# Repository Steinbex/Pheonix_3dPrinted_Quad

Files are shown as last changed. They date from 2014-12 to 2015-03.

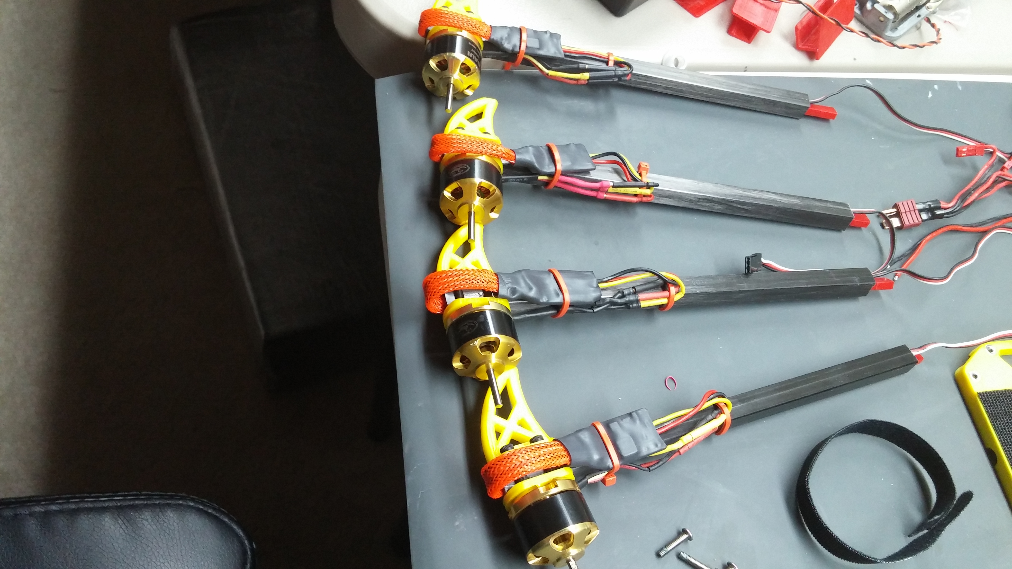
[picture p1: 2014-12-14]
Manual/Images/20141213_224951.jpg

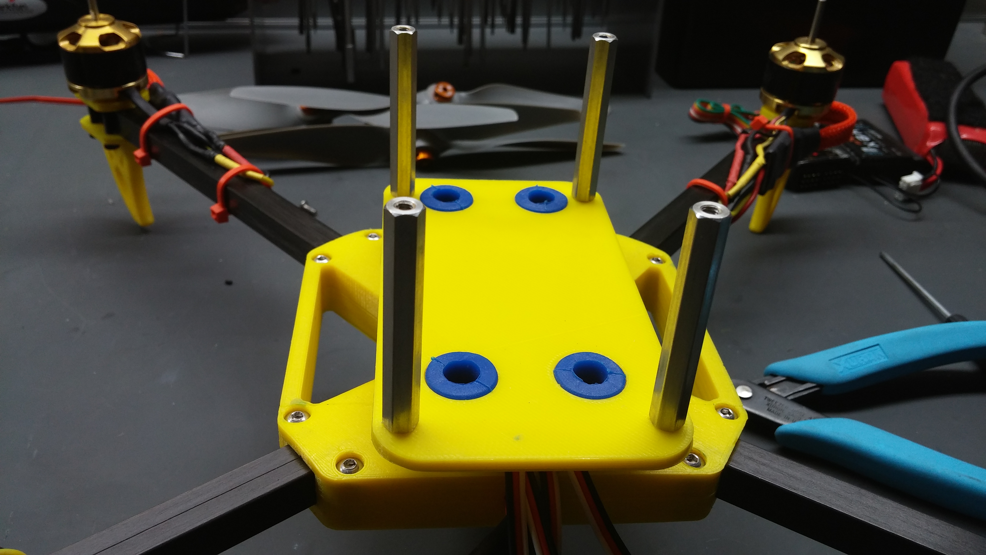
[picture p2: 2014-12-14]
Manual/Images/20141213_233334.jpg

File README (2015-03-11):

Here is the quad frame that, along with a 3d printer, never dies. This durable frame is the result of about a dozen iterations that have led to this lightweight, clean and dirty plate design, that can be built with nearly all 3d printed components. I release it here under the apache license with the intent that we can all grow this together to try and make a constantly improving quad. 

To BUILD:
Print 
4x bottom motor mounts
4x top motor mounts
1x Center Section-1
1x Center Section-2 

For FPV Add:
1x Center Section-1
1x Center Section-2

Non-Printed Hardware:
Main Frame:
16x m3x0.5x18mm Socket Head Cap Screws McMaster 92095A472 for the motor mounts
15x m3x0.5x14mm Socket Head Cap Screws McMaster 92095A168 for the center section
15x m3x0.5 Hex Nut McMaster 90591A121
4x 10mmx200mm Carbon Square Tube Hobbyking 0780000006-0

Clean Plate:
8x M3x0.5x6mm Socket head cap screws McMaster 92095A179 for attaching the plates to the standoffs
4x M3 x 45mm Standoffs McMaster 95947A272 for Clean Plate
4x Vibration Dampeners Hobbyking 450000030-0 for clean plate

Recommended flying specs:
3s 2200 maH Lipo battery
1100 kv Motors
10-15a speed controllers
8x4.5 props

TODO:
More complete Mechanical BOM
Electrical BOM

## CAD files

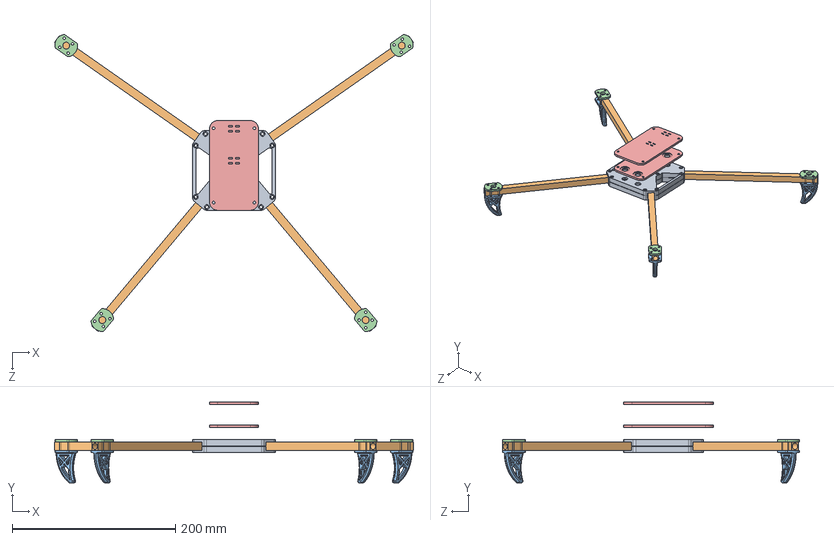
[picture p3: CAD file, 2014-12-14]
Model Files/Pheonix Quad.SLDASM
439.9 x 99.0 x 363.8 mm
Center Section x 2
Carbon Arm x 4
Bottom Motor Mount x 4
Top Motor Mount x 4
Clean Plate x 2

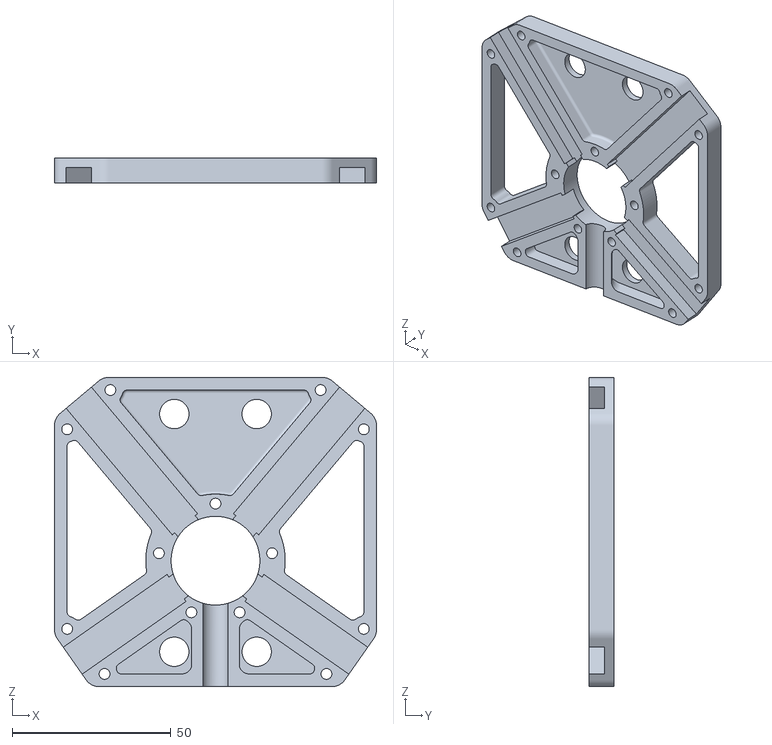
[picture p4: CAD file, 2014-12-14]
Build Files/Carbon Arm Quad - Center Section-2.STL
101.6 x 7.75 x 97.6

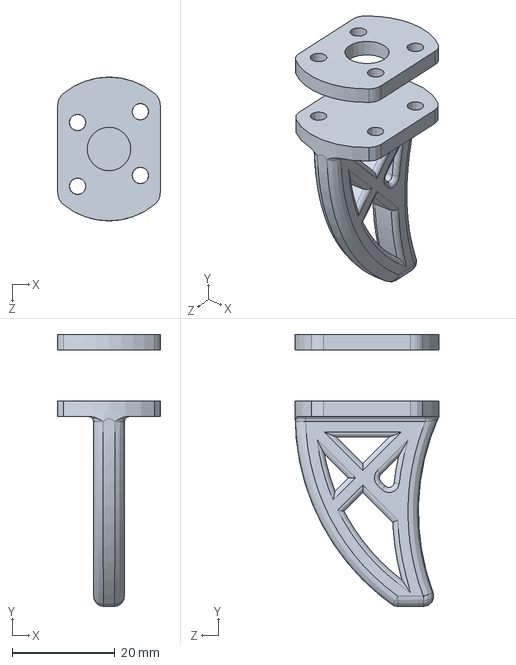
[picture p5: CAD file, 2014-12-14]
Model Files/V2 Motor Mount.SLDPRT
20.0 x 53.0 x 28.0 mm

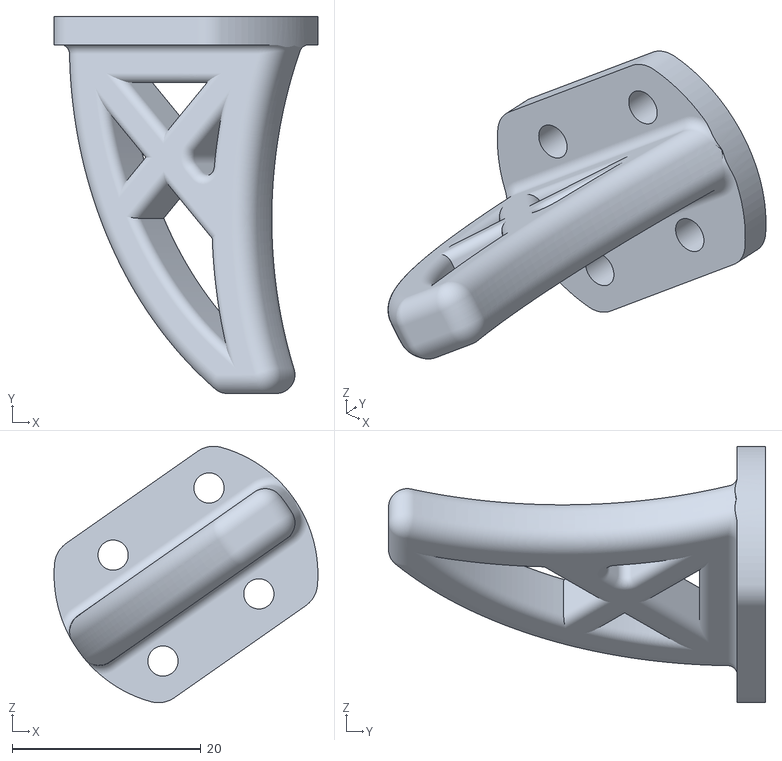
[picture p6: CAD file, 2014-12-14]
Build Files/Carbon Arm Quad - Bottom Motor Mount-1.STL
28.0 x 40.0 x 27.2

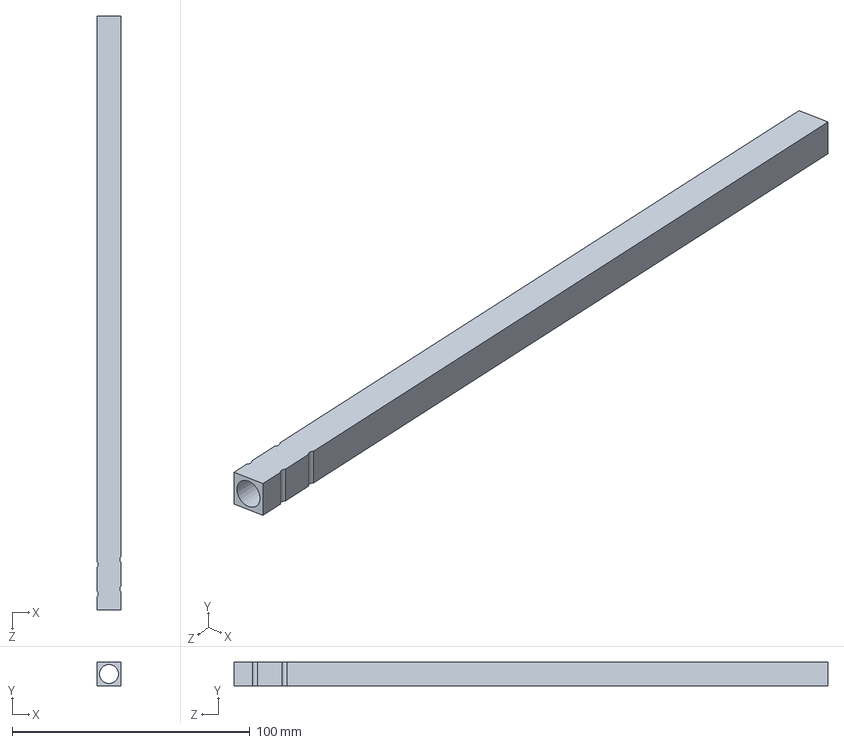
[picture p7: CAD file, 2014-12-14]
Model Files/Carbon Arm.SLDPRT
10.0 x 10.0 x 250.0 mm

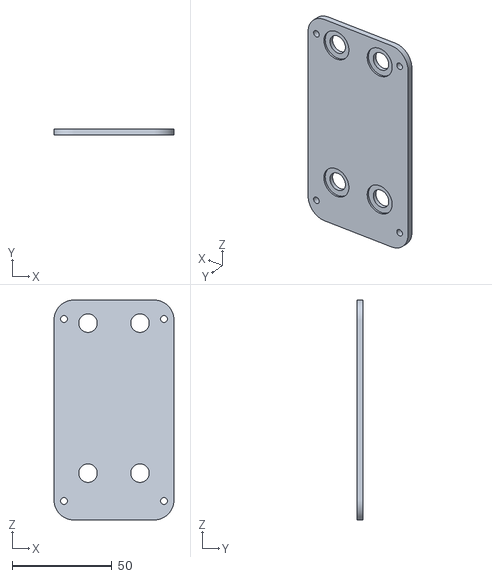
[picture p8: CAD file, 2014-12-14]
Build Files/Carbon Arm Quad - Clean Plate-1.STL
60.0 x 3.00 x 110.0

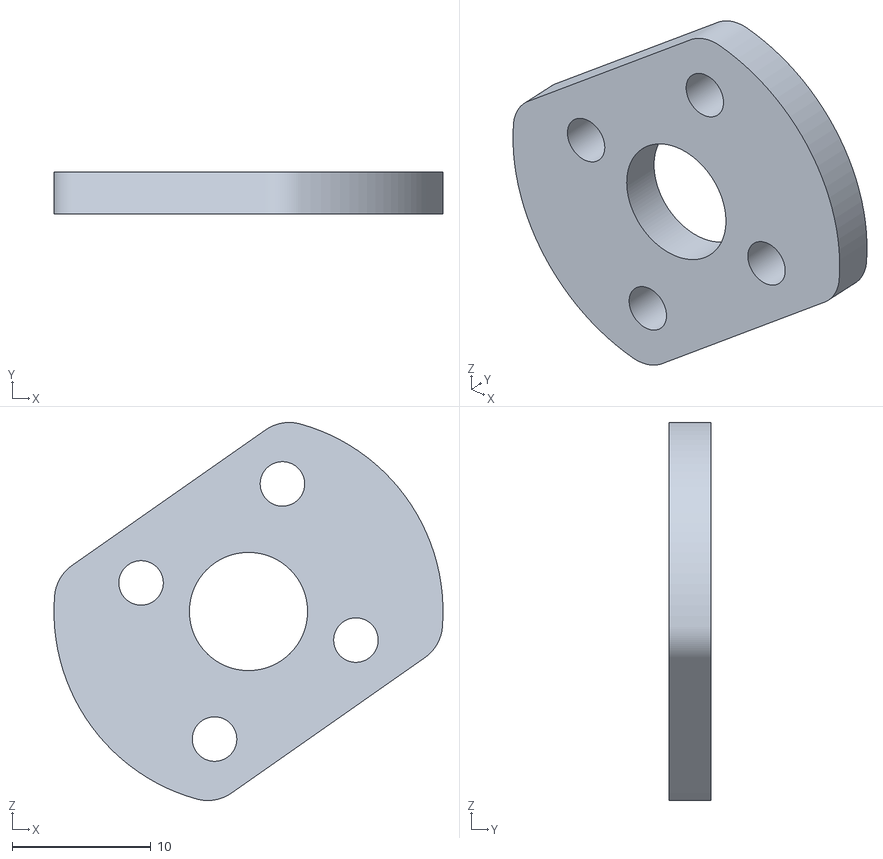
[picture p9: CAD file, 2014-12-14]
Build Files/Carbon Arm Quad - Top Motor Mount-1.STL
28.0 x 3.00 x 27.2

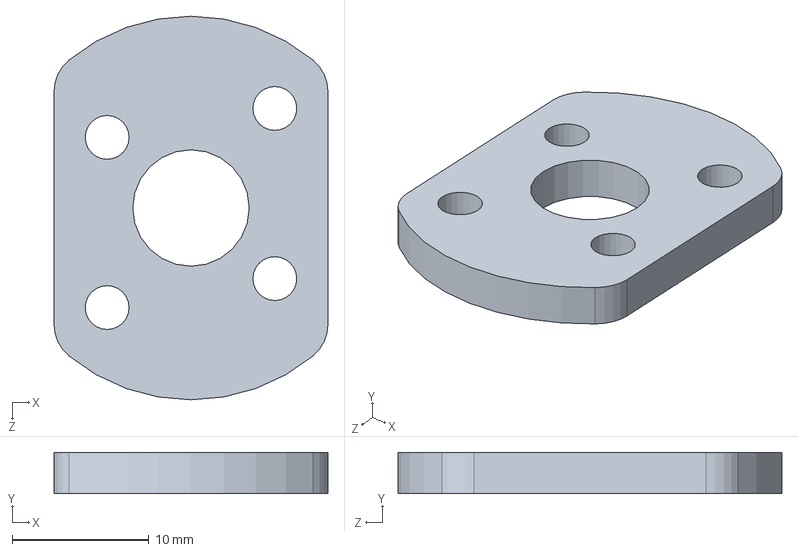
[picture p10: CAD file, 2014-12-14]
Model Files/Top Motor Mount.sldprt
20.0 x 3.00 x 28.0 mm

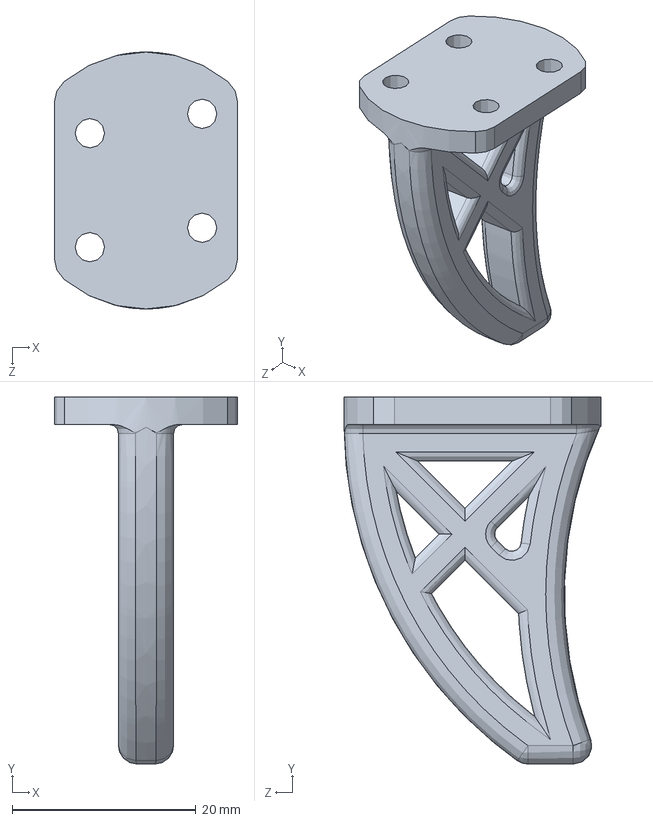
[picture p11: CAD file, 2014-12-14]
Model Files/Bottom Motor Mount.sldprt
20.0 x 40.0 x 28.0 mm

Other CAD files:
Model Files/Clean Plate.SLDPRT
Build Files/Carbon Arm Quad - Center Section-1.STL
Build Files/Carbon Arm Quad - Clean Plate-2.STL
Model Files/Center Section.SLDPRT

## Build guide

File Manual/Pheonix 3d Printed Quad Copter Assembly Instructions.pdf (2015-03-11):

# Pheonix 3d Printed Quad Copter Assembly Instructions

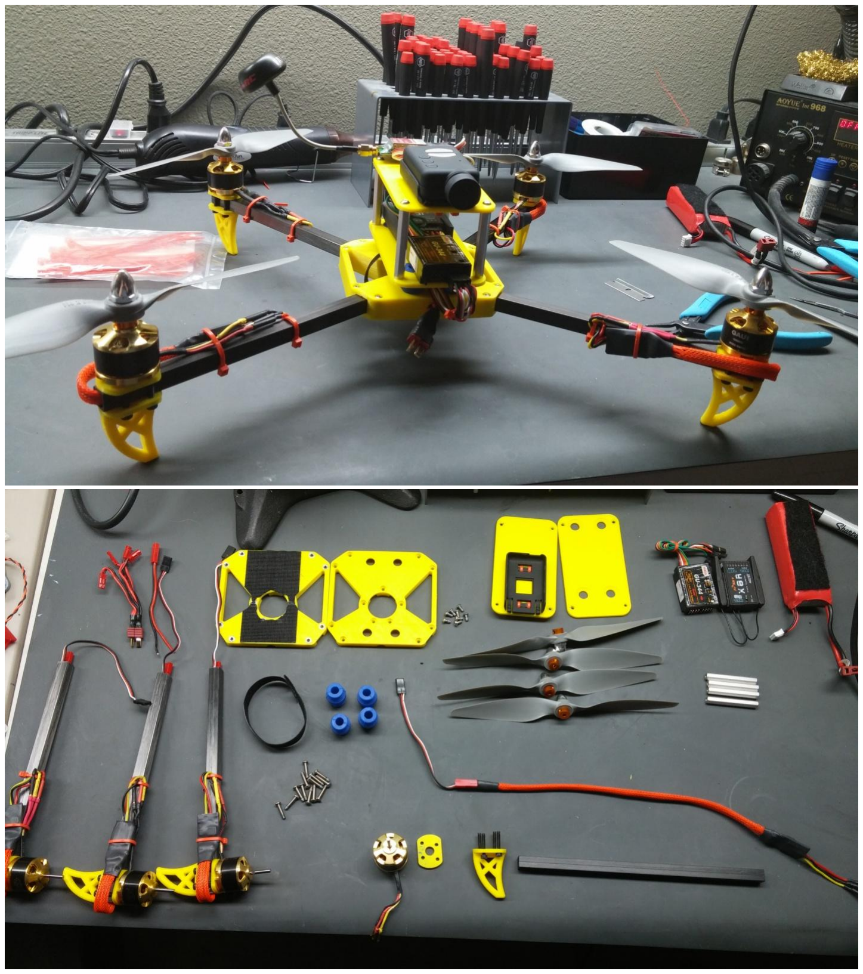
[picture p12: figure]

### Arm Assembly:

To begin the assembly we will start by assembling one of the arms. Start by taking one of the carbon booms and, using a rat tail file make clearance for the screws to go around the bar as in the picture.

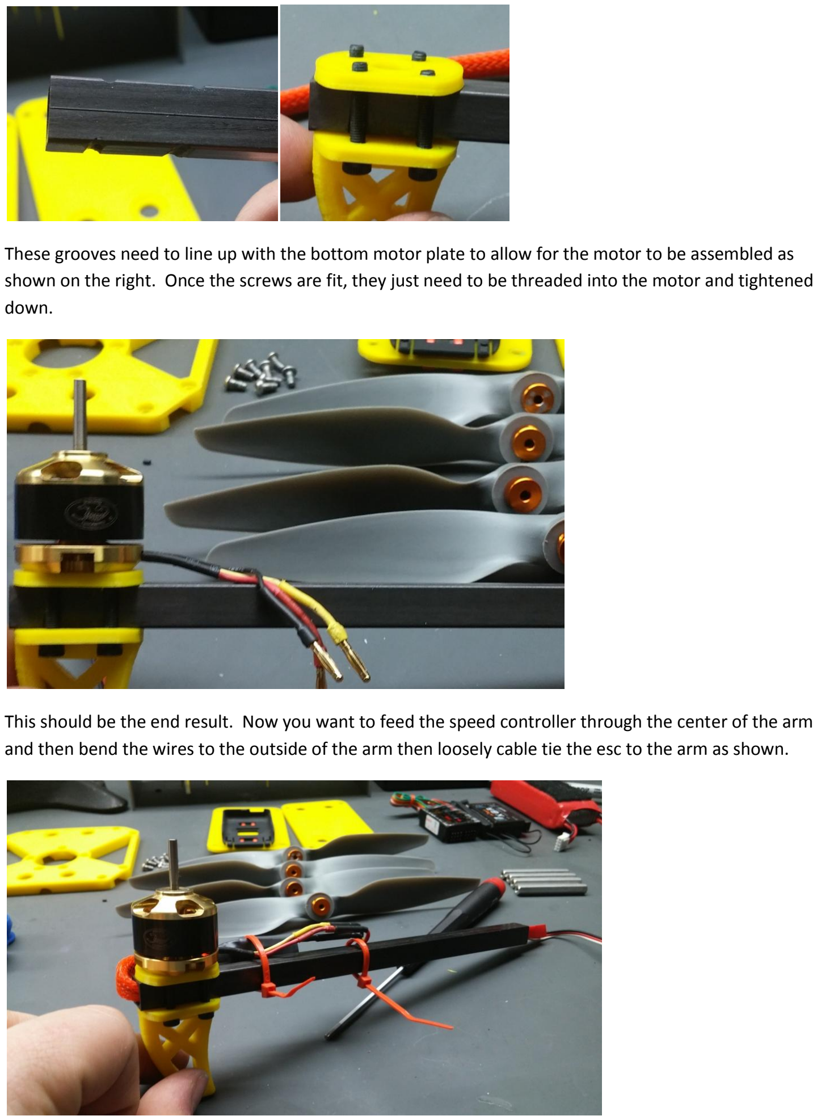
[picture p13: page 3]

These grooves need to line up with the bottom motor plate to allow for the motor to be assembled as shown on the right. Once the screws are fit, they just need to be threaded into the motor and tightened down.

This should be the end result. Now you want to feed the speed controller through the center of the arm and then bend the wires to the outside of the arm then loosely cable tie the esc to the arm as shown.

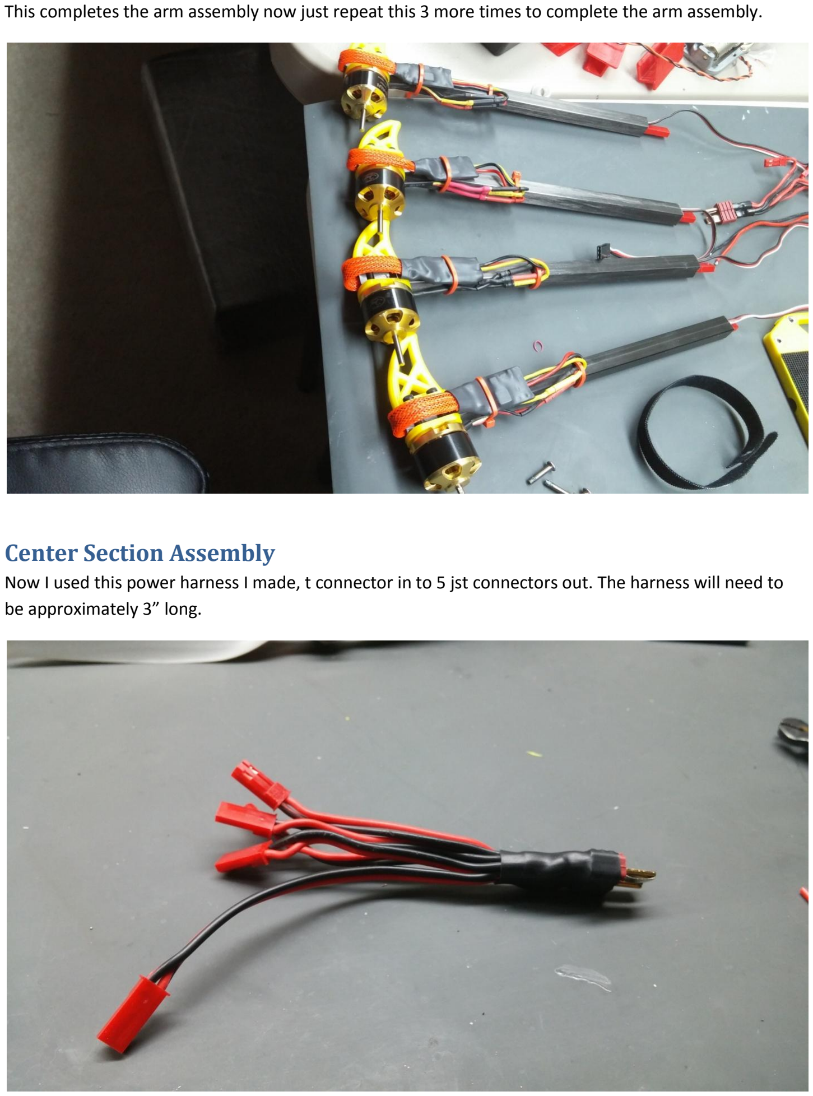
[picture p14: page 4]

This completes the arm assembly now just repeat this 3 more times to complete the arm assembly.

### Center Section Assembly

Now I used this power harness I made, t connector in to 5 jst connectors out. The harness will need to be approximately 3” long.

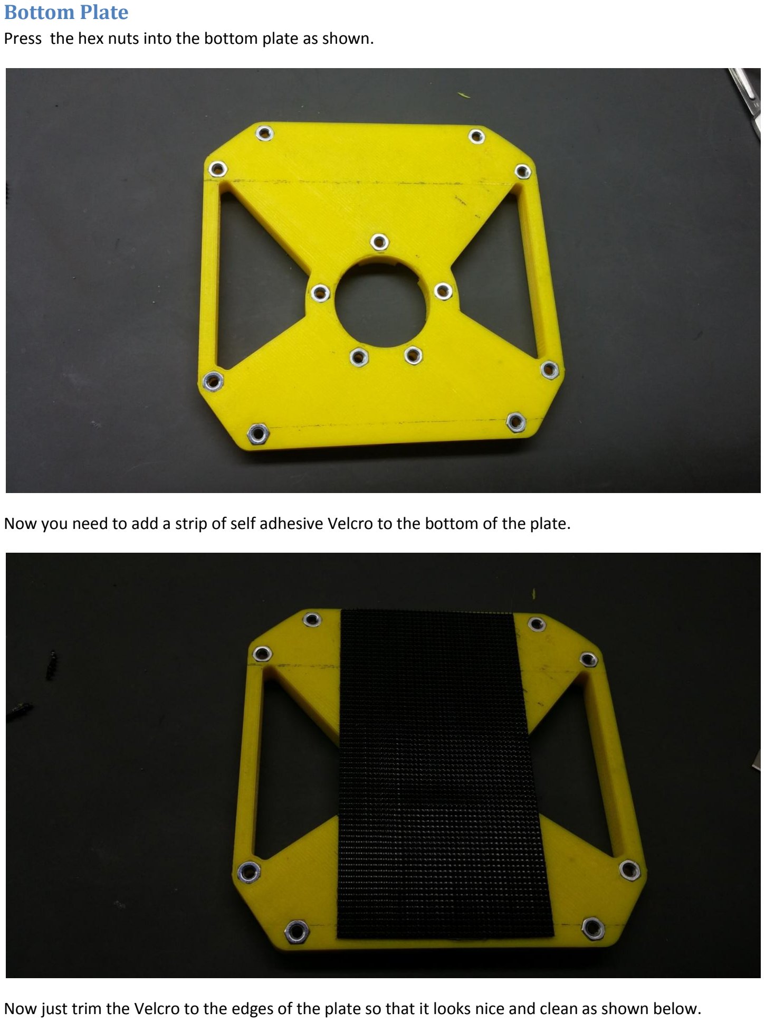
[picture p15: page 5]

### Bottom Plate

Press the hex nuts into the bottom plate as shown.

Now you need to add a strip of self adhesive Velcro to the bottom of the plate.

Now just trim the Velcro to the edges of the plate so that it looks nice and clean as shown below.

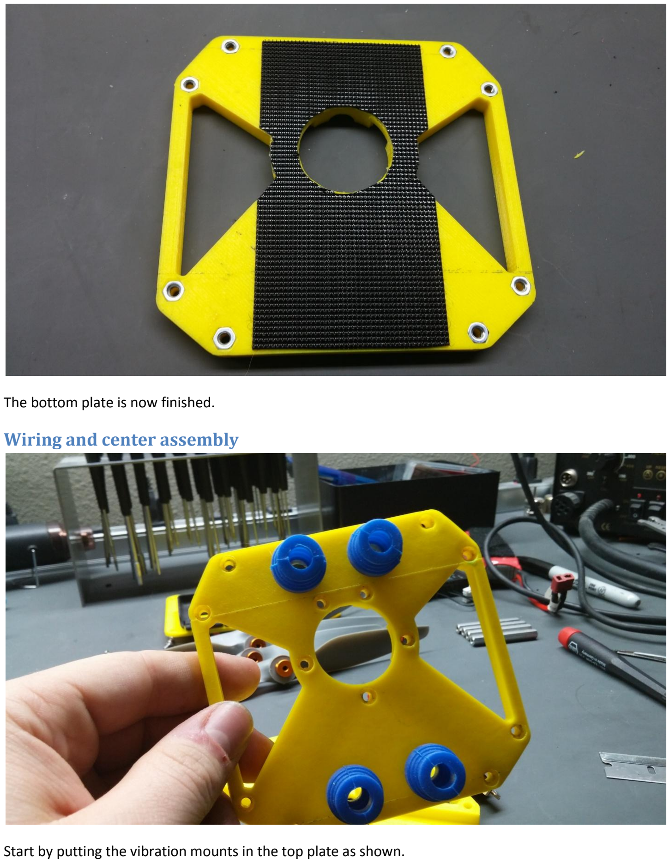
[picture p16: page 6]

The bottom plate is now finished.

### Wiring and center assembly

Start by putting the vibration mounts in the top plate as shown.

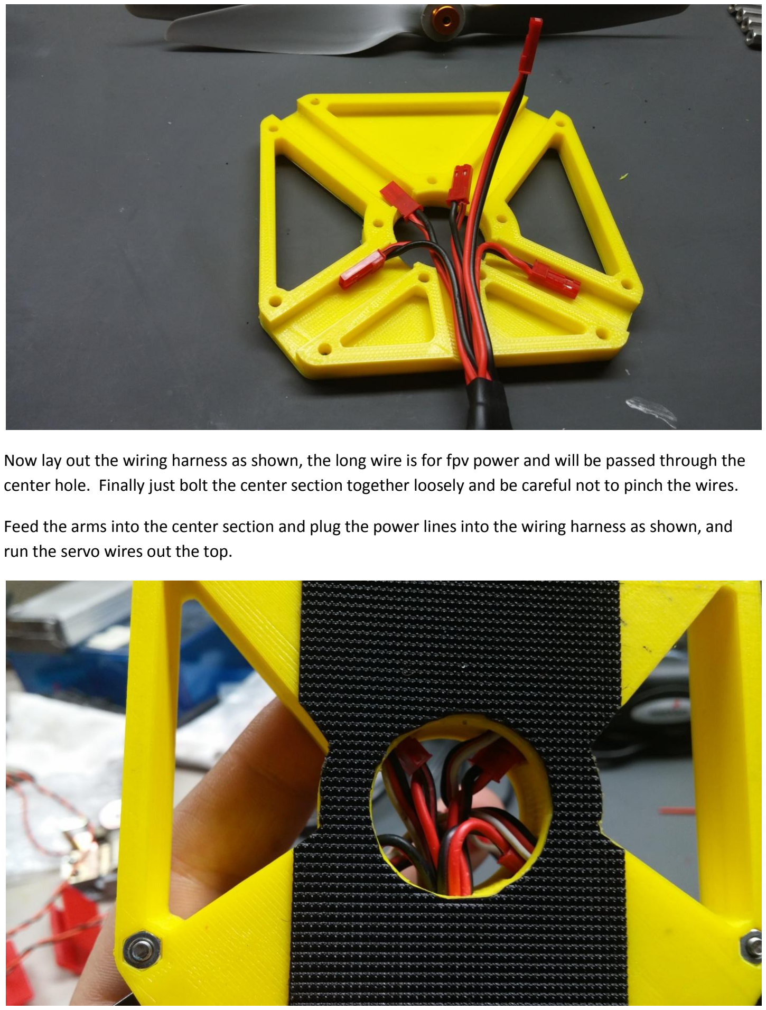
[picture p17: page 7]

Now lay out the wiring harness as shown, the long wire is for fpv power and will be passed through the center hole. Finally just bolt the center section together loosely and be careful not to pinch the wires.

Feed the arms into the center section and plug the power lines into the wiring harness as shown, and run the servo wires out the top.

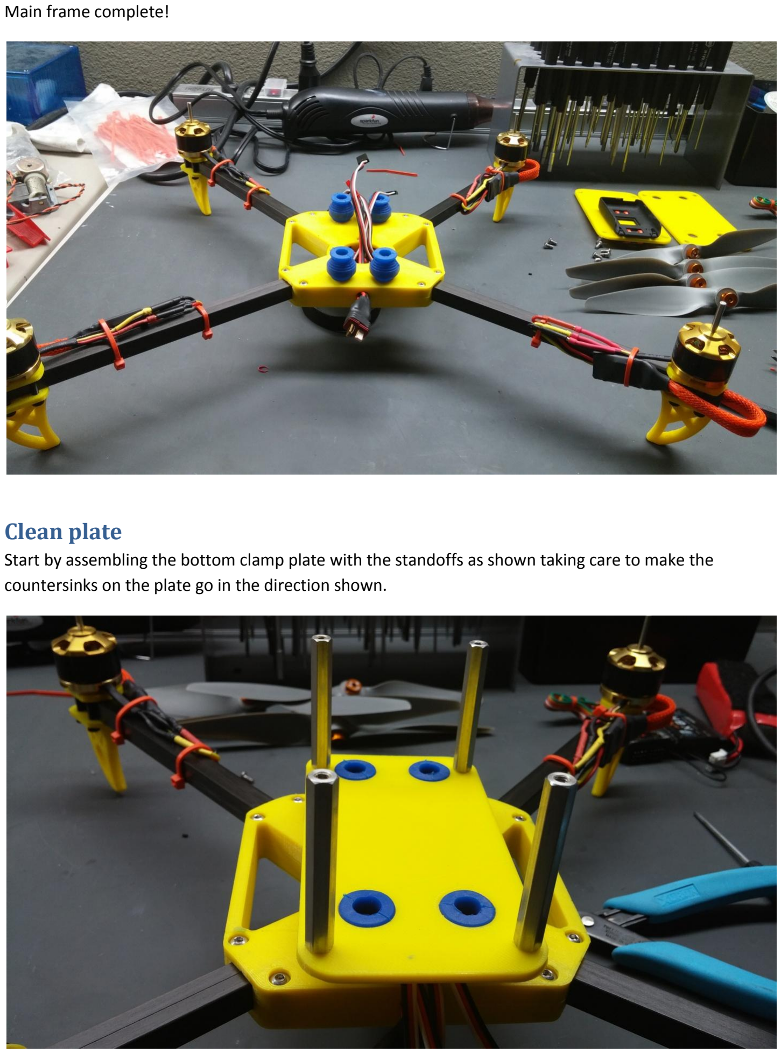
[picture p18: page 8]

Main frame complete!

### Clean plate

Start by assembling the bottom clamp plate with the standoffs as shown taking care to make the countersinks on the plate go in the direction shown.

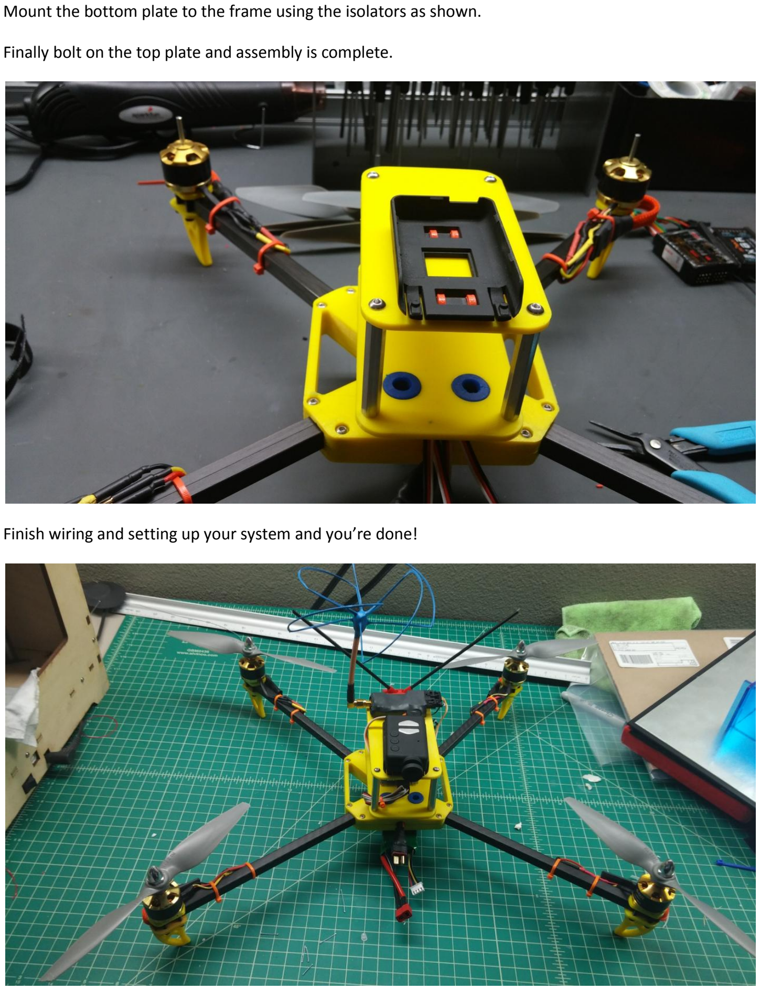
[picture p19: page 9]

Mount the bottom plate to the frame using the isolators as shown.

Finally bolt on the top plate and assembly is complete.

Finish wiring and setting up your system and you’re done!

### Updates:

1. Since the initial build I have now switched the arms to the woven carbon arms found on rcexplorer.se and it is much more tough. There are no changes to the instructions.
2. The Gaui controller is antiquated, and I knew that from the beginning. I have since switched to the Naze32 which is so much better, just solid and reliable.

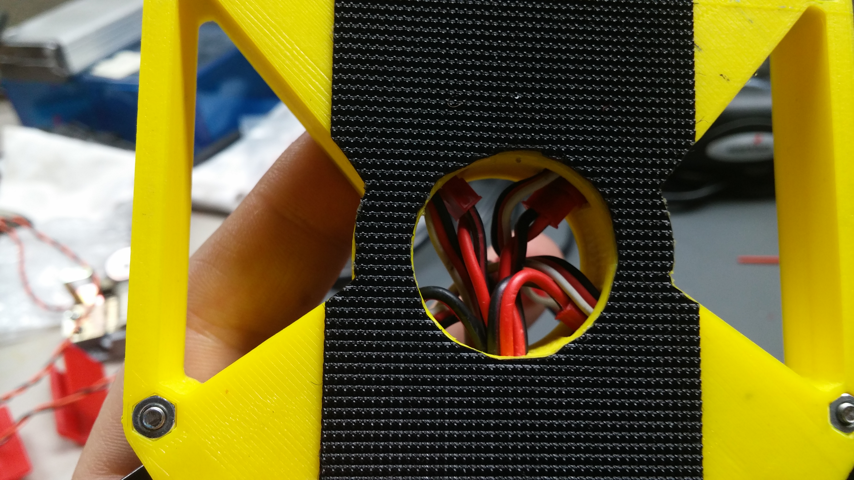
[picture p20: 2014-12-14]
Manual/Images/20141213_232949.jpg

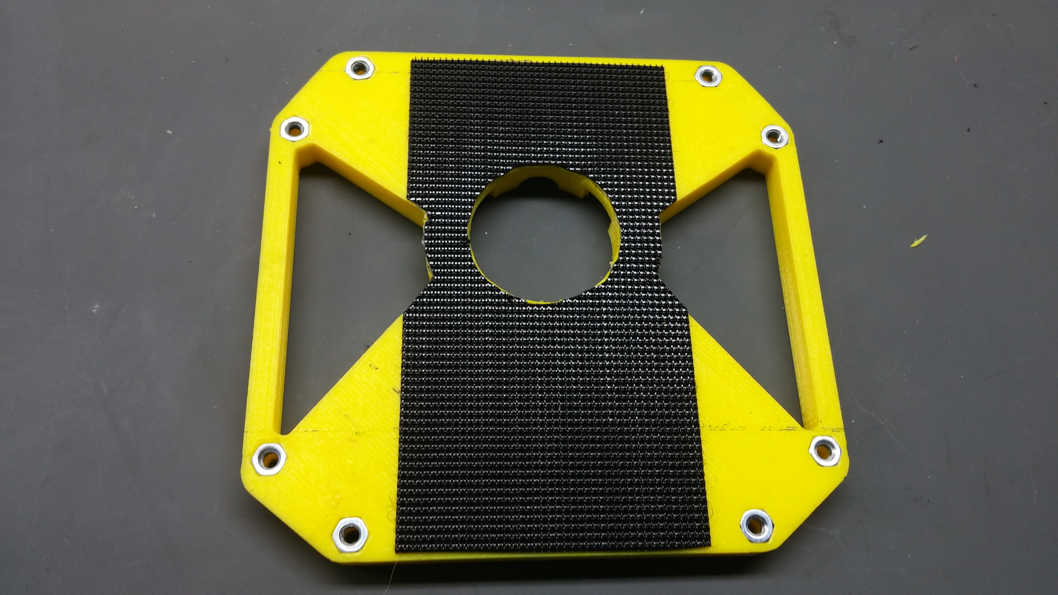
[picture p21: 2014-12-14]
Manual/Images/20141213_231440.jpg

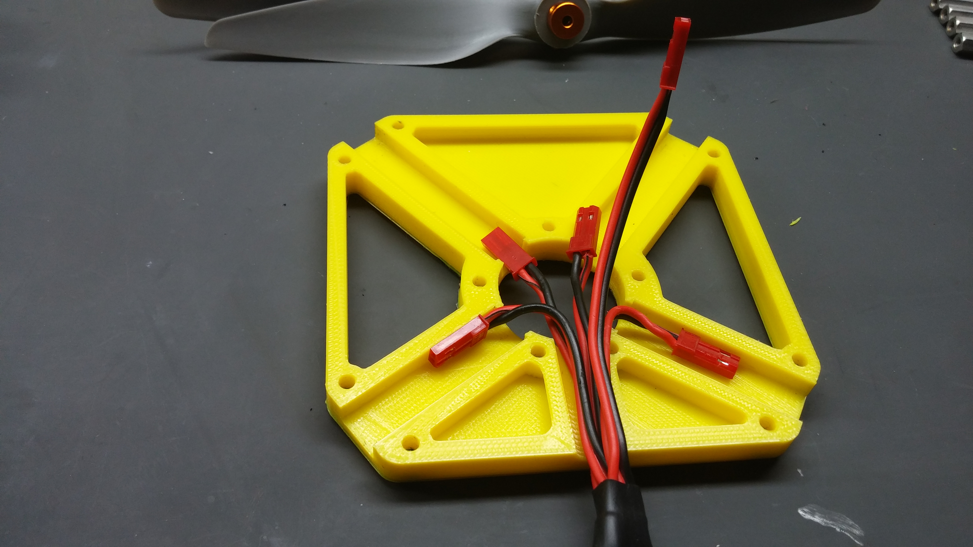
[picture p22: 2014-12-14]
Manual/Images/20141213_231509.jpg

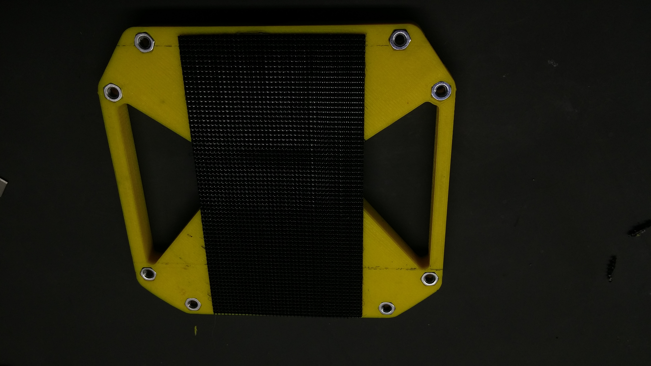
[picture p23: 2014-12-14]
Manual/Images/20141213_231152.jpg
